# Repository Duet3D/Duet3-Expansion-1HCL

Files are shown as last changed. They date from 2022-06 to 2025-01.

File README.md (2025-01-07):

# Duet 3 Expansion 1HCL
The Duet 3 Expansion 1HCL is a CAN-FD connected expansion board for the [Duet 3 Mainboard 6HC](https://www.duet3d.com/duet3mainboard6hc), [Duet 3 Mainboard 6XD](https://www.duet3d.com/duet3mainboard6xd) and [Duet 3 Mini 5+](https://www.duet3d.com/duet3mini5plus) that is designed to provide a high current stepper motor driver, combined with multiple interfaces for position feedback. It has a number of peripheral inputs and outputs for functions such as sensing motor temperature, controlling a brake and axis endstop.

Image of Duet 3 Expansion 1HCL

Product page is here: https://www.duet3d.com/duet-3-expansion-1hcl

Documentation is here: https://docs.duet3d.com/Duet3D_hardware/Duet_3_family/Duet_3_Expansion_1HCL

As always please discuss this on the Duet3d forum: https://forum.duet3d.com/

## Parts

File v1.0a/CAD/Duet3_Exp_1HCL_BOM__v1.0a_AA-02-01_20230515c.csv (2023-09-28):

Source: | G:\My Drive\Duet\Duet3\Duet3 Expansion 1HCL\Duet3_Expansion_1HCL_v1.0a-AA-02-01\Duet3_Exp_1HCL.kicad_sch
Date: | 15/05/2023 18:52:26
Tool: | Eeschema (6.0.0)
Generator: | C:\Program Files\KiCad\bin\scripting\plugins/bom_csv_grouped_by_value_d3d.py
Component Count: | 204
Collated Components:
Item | Value | Qty | LibPart | Footprint | Reference(s) | Datasheet | Frequency | Part Number | Rating
1 | 2u2 16V 10% X5R | 4 | Device:C_Small | Capacitor_SMD:C_0603_1608Metric_Wbry | C1, C2, C26, C41 | ~ |  | CL10A225KO8NNNC
2 | 0u1 10V 10% X7R | 8 | Device:C_Small | Capacitor_SMD:C_0402_1005Metric_Wbry | C3, C4, C6, C40, C42, C44, C47, C49 | ~ |  | CL05B104KP5NNNC
3 | 470n 16V 10% X7R | 1 | Device:C_Small | Capacitor_SMD:C_0603_1608Metric_Wbry | C5 | ~ |  | CL10B474KO8NNNC
4 | 10n 25V 10% X7R | 5 | Device:C_Small | Capacitor_SMD:C_0402_1005Metric_Wbry | C7, C30, C39, C51, C63 | ~ |  | CL05B103KA5VPNC
5 | 2n2 50V 10% X7R | 2 | Device:C_Small | Capacitor_SMD:C_0402_1005Metric_Wbry | C8, C10 | ~ |  | GCM155R71H222KA37D
6 | 220n 16V 10% X7R | 4 | Device:C_Small | Capacitor_SMD:C_0603_1608Metric_Wbry | C9, C11, C14, C15 | ~ |  | CL10B224KO8NNNC
7 | 0u1 50V 10% X7R | 1 | Device:C_Small | Capacitor_SMD:C_0603_1608Metric_Wbry | C12 | ~ |  | CL10B104KB8NNNC
8 | 22n 100V 10% X7R | 1 | Device:C_Small | Capacitor_SMD:C_0603_1608Metric_Wbry | C13 | ~ |  | C0603C223K1RACTU
9 | 0u1 100V 10% X7R | 2 | Device:C_Small | Capacitor_SMD:C_0603_1608Metric_Wbry | C16, C34 | ~ |  | HMK107B7104MA-T or similar
10 | 220u 63V | 2 | Device:CP1_Small | Capacitor_SMD:CP_Elec_12.5x14 | C17, C53 |  |  | 865060762009
11 | 220n 100V 10% X7R | 4 | Device:C_Small | Capacitor_SMD:C_1206_3216Metric | C18, C19, C20, C21 | ~ |  | C3216X7R2A224K115AA
12 | 1n 100V 10% X7R | 4 | Device:C_Small | Capacitor_SMD:C_0603_1608Metric_Wbry | C22, C23, C24, C25 | ~ |  | CGA3E2X7R2A102K080AA
13 | 2u2 6.3V 10% X7R | 4 | Device:C_Small | Capacitor_SMD:C_0402_1005Metric_Wbry | C28, C50, C52, C55 | ~ |  | CC0603KRX7R5BB225
14 | 2u2 100V 10% X7R | 4 | Device:C_Small | Capacitor_SMD:C_1210_3225Metric | C29, C32, C35, C64 | ~ |  | CL32B225KCJSNNE
15 | 1u 16V 10% X7R | 4 | Device:C_Small | Capacitor_SMD:C_0603_1608Metric_Wbry | C31, C36, C38, C56 | ~ |  | CL10B105KO8NNNC
16 | 22u 100V | 1 | Device:CP1 | Capacitor_SMD:CP_Elec_8x10 | C33 |  |  | EEE-2AA220UP or similar
17 | 4u7 16V 10% X7S | 2 | Device:C_Small | Capacitor_SMD:C_1206_3216Metric | C37, C62 | ~ |  | GRM21BR71C475KE51K
18 | 10u 16V 10% X7R | 2 | Device:C_Small | Capacitor_SMD:C_0805_2012Metric | C43, C48 | ~ |  | CL21B106KOQNNNE
19 | 22p 16V 5% C0G,NP0 | 2 | Device:C_Small | Capacitor_SMD:C_0402_1005Metric_Wbry | C45, C46 | ~ |  | C0402C220J4GACTU
20 | 10n 25V 10% X7R | 1 | Duet3:C_SMALL | Capacitor_SMD:C_0402_1005Metric_Wbry | C57 |  |  | CL05B103KA5VPNC
21 | 10u 16V 10% X7R | 1 | Duet3:C_SMALL | Capacitor_SMD:C_0805_2012Metric | C58 |  |  | CL21B106KOQNNNE
22 | 0u1 10V 10% X7R | 1 | Duet3:C_SMALL | Capacitor_SMD:C_0402_1005Metric_Wbry | C59 |  |  | CL05B104KP5NNNC
23 | 22u 25V 20% X5R | 2 | Duet3:C_SMALL | Capacitor_SMD:C_0805_2012Metric | C60, C61 |  |  | GRM21BR61E226ME44L
24 | BAT40V | 4 | Diode:BAT40V | Package_TO_SOT_SMD:SOT-563 | D1, D2, D3, D4 |  |  | BAT40V-7
25 | BAT54C | 3 | Diode:BAT54C | Package_TO_SOT_SMD:SOT-23 | D6, D18, D19 | http://www.diodes.com/_files/datasheets/ds11005.pdf |  | BAT54CLT1G
26 | 60V+ 1A+ | 3 | Device:D_Schottky | Diode_SMD:D_SMF | D7, D8, D10 | ~ |  | SS1FH10-M3/H or equivalent
27 | 12V+ | 1 | Device:LED | LED_SMD:LED_0603_1608Metric | D9 | ~ |  | 150060AS75000 or equivalent Amber
28 | V_FUSED | 1 | Device:LED | LED_SMD:LED_0603_1608Metric | D11 | ~ |  | 150060BS75000 or equivalent Blue
29 | 5V+ | 1 | Device:LED | LED_SMD:LED_0603_1608Metric | D12 | ~ |  | 150060RS75000 or equivalent Red
30 | STATUS | 1 | Device:LED | LED_SMD:LED_0603_1608Metric | D13 | ~ |  | 150060RS75000 or equivalent Red
31 | ACT | 1 | Device:LED | LED_SMD:LED_0603_1608Metric | D14 | ~ |  | 150060VS75000 or equivalent Green
32 | D_TVS_5V | 1 | Device:D_Zener_Small | Diode_SMD:DFN1610-2L | D15 | ~ |  | 824032815 or 824031815
33 | D_TVS_3.3V | 1 | Device:D_Zener_Small | Diode_SMD:DFN1610-2L | D16 | ~ |  | 824032813
34 | 3.3V+ | 1 | Device:LED | LED_SMD:LED_0603_1608Metric | D17 | ~ |  | 150060VS75000 or equivalent Green
35 | V_FUSED | 1 | Device:Fuse_Small | complib:MCCQ-122-minibladefuseholder | F1 | ~ |  | Fit with 5A Fuse
36 | VB_FUSED | 1 | Device:Fuse_Small | complib:MCCQ-122-minibladefuseholder | F2 | ~ |  | Fit with 5A Fuse
37 | VSSA FUSE | 1 | Device:Fuse | Fuse:Fuse_1206_3216Metric | F3 | ~ |  | 0ZCJ0020FF2E
38 | VIN | 1 | Connector_Generic:Conn_01x02 | complib:screwt-barrier-9.5mm-1x2 | J1 | ~ |  | HB950-9.50-2P
39 | OUT_0 | 1 | Connector_Generic:Conn_01x02 | Connector_Molex:Wurth_61900211121-1x02_P2.54mm_Vertical-(Molex_KK-254_AE-6410-02Acompatible) | J2 | ~ |  | 61900211121
40 | OUT_1 | 1 | Connector_Generic:Conn_01x02 | Connector_Molex:Wurth_61900211121-1x02_P2.54mm_Vertical-(Molex_KK-254_AE-6410-02Acompatible) | J3 | ~ |  | 61900211121
41 | V_BRAKE | 1 | Connector_Generic:Conn_01x02 | Connector_JST:JST_VH_B2P-VH_1x02_P3.96mm_Vertical | J4 | ~ |  | B2P-VH(LF)(SN)
42 | IO_0 | 1 | Connector_Generic:Conn_01x05 | Connector_Molex:Wurth_61900511121-1x05_P2.54mm_Vertical(Molex_KK-254_AE-6410-05A_Compatibe) | J5 | ~ |  | 61900511121
43 | IO_1 | 1 | Connector_Generic:Conn_01x05 | Connector_Molex:Wurth_61900511121-1x05_P2.54mm_Vertical(Molex_KK-254_AE-6410-05A_Compatibe) | J6 | ~ |  | 61900511121
44 | OUT_0 Select V | 1 | Connector_Generic:Conn_01x03 | Connector_PinHeader_2.54mm:PinHeader_1x03_P2.54mm_Vertical | J7 | ~ |  | THS-03-R
45 | Q IN | 1 | Connector_Generic:Conn_01x05 | Connector_Molex:Wurth_61900511121-1x05_P2.54mm_Vertical(Molex_KK-254_AE-6410-05A_Compatibe) | J8 | ~ |  | 61900511121
46 | SPI | 1 | Connector_Generic:Conn_02x05_Odd_Even | Connector_IDC:IDC-Header_2x05_P2.54mm_Vertical | J9 | ~ |  | 61201021621
47 | SWD | 1 | Connector_Generic:Conn_01x06 | complib:JST_ZH_1x06_P1.5_B6B-ZR-SM4-TF | J10 | ~ |  | B6B-ZR(LF)(SN)
48 | DRIVER | 1 | Connector_Generic:Conn_01x04 | Connector_JST:JST_VH_B4P-VH_1x04_P3.96mm_Vertical | J11 | ~ |  | B4P-VH(LF)(SN)
49 | TEMP_0 | 1 | Connector_Generic:Conn_01x02 | Connector_Molex:Wurth_61900211121-1x02_P2.54mm_Vertical-(Molex_KK-254_AE-6410-02Acompatible) | J12 | ~ |  | 61900511121
50 | CAN_IN | 1 | Duet3:RJ12-Connector_Specialized | complib:RJ11_6P6C_half_shield | J13 |  |  | Wurth 615 006 143 421 or equivalent
51 | CAN_OUT | 1 | Duet3:RJ12-Connector_Specialized | complib:RJ11_6P6C_half_shield | J14 |  |  | Wurth 615 006 143 421 or equivalent
52 | OUT_1 Select V | 1 | Connector_Generic:Conn_01x03 | Connector_PinHeader_2.54mm:PinHeader_1x03_P2.54mm_Vertical | J15 | ~ |  | THS-03-R
53 | TEMP_1 | 1 | Connector_Generic:Conn_01x02 | Connector_Molex:Wurth_61900211121-1x02_P2.54mm_Vertical-(Molex_KK-254_AE-6410-02Acompatible) | J16 | ~ |  | 61900511121
54 | Term_R | 1 | Duet3:Jumper_4_Open | Connector_PinHeader_2.54mm:PinHeader_1x04_P2.54mm_Vertical | JP1 | ~ |  | THS-04-R
55 | CAN RESET | 1 | Device:Jumper_NO_Small | Connector_PinHeader_2.54mm:PinHeader_1x02_P2.54mm_Vertical | JP2 |  |  | THS-02-R
56 | IO1_I2C | 1 | Device:Jumper_NO_Small | Connector_PinHeader_2.54mm:PinHeader_1x02_P2.54mm_Vertical | JP3 |  |  | THS-02-R
57 | CM Choke | 1 | Duet3:L_Coupled_v2 | complib:Wurth_CM_Choke_1812_744235nnn | L1 | ~ |  | 744235110
58 | 4.7uH | 1 | Device:L_Small | Inductor_SMD:L_0805_2012Metric | L2 | ~ |  | MBKK2012T4R7M or CB2012T4R7M or similar
59 | 120R @100mHz | 2 | Device:L_Small | Inductor_SMD:L_0402_1005Metric | L3, L5 | ~ |  | 7427927311 or similar
60 | 100u | 1 | Device:L_Small | Inductor_SMD:L_Taiyo-Yuden_NR-60xx | L4 | ~ |  | NR6028T101M | >0.5A, >0.6A saturation, shielded, <0R85 DCR
61 | 1K @100Mhz | 1 | Device:L_Small | Inductor_SMD:L_0603_1608Metric | L6 | ~ |  | 742792662 or PE-0603FB102ST or similar
62 | 100 ohm, 4 A | 2 | Duet3:L_MINI | Inductor_SMD:L_0805_2012Metric | L7, L9 |  |  | 742792025 or MPZ2012S101A or similar
63 | 10u | 1 | Duet3:L_MINI | Inductor_SMD:L_Wuerth_7440405xxxx | L8 |  |  | 74404054100 or NR5040T100M
64 | FID | 2 | Duet3:FID | Fiducial:Fiducial_1mm_Mask2mm | M1, M2 |  |  | virtual component - DNP
65 | MOUNTING | 4 | Mechanical:MountingHole | MountingHole:MountingHole_3.2mm_M3 | M3, M4, M5, M6 | ~ |  | virtual component - DNP
66 | Duet3D_Logo | 1 | Duet3:Duet3D_Logo | complib:LOGO_NEW_Duet3D_vertical_6mm | M7 |  |  | virtual component - DNP
67 | GNDANA-GND NET TIE | 1 | Device:Net-Tie_2 | NetTie:NetTie-2_SMD_Pad0.5mm | NT1 |  |  | virtual component - DNP
68 | SIZ250DT | 4 | Duet3:SIZ250DT | complib:Vishay_PowerPAIR3x3S | Q1, Q2, Q3, Q4 | https://www.infineon.com/dgdl/irfi4019h-117p.pdf?fileId=5546d462533600a401535623d74d1f6f |  | SIZ250DT-T1-GE3
69 | DMN6040SVT | 2 | Duet3:DMN6040SVT | Package_TO_SOT_SMD:SOT-23-6-DMN6040SVT | Q5, Q6 | https://www.diodes.com/assets/Datasheets/DMN6040SVT.pdf |  | DMN6040SVT
70 | 2R2 1% 0.063W | 1 | Device:R_Small | Resistor_SMD:R_0402_1005Metric_Wbry | R1 | ~ |  | RMCF0402FT2R20
71 | 59R 1% 0.063W | 2 | Device:R_Small | Resistor_SMD:R_0402_1005Metric_Wbry | R2, R3 | ~ |  | RMCF0402FT59R0
72 | 47R 1% 0.063W | 4 | Device:R_Small | Resistor_SMD:R_0603_1608Metric_Wbry | R4, R5, R6, R7 | ~ |  | RMCF0402FT47R0
73 | 150R 1% 0.063W | 8 | Device:R_Small | Resistor_SMD:R_0402_1005Metric_Wbry | R8, R9, R10, R11, R12, R13, R14, R15 | ~ |  | RMCF0402FT150R
74 | 0R05 1% 1W | 2 | Duet3:R_SenseKelvin | complib:R_1206_SenseResistorKelvin | R16, R17 |  |  | PE1206FRE470R05L or ERJ-8CWFR050V or similar
75 | 10K 1% 0.1W | 19 | Device:R_Small | Resistor_SMD:R_0402_1005Metric_Wbry | R18, R19, R20, R21, R22, R27, R38, R39, R42, R43, R46, R47, R64, R65, R66, R67, R68, R69, R72 | ~ |  | RK73H1ETTP1002F
76 | 27R 1% 0.063W | 1 | Device:R_Small | Resistor_SMD:R_0402_1005Metric_Wbry | R23 | ~ |  | CRGCQ0402F27R
77 | 470R 1% 0.063W | 5 | Device:R_Small | Resistor_SMD:R_0402_1005Metric_Wbry | R24, R25, R45, R49, R57 | ~ |  | RC0402FR-07470RL
78 | 4K7 1% 0.063W | 2 | Device:R_Small | Resistor_SMD:R_0402_1005Metric_Wbry | R26, R50 | ~ |  | RK73H1ETTP4701F
79 | 100K 1% 0.063W | 2 | Device:R_Small | Resistor_SMD:R_0402_1005Metric_Wbry | R28, R34 | ~ |  | RMCF0402FT100K
80 | 5K1 1% 0.063W | 1 | Device:R_Small | Resistor_SMD:R_0402_1005Metric_Wbry | R29 | ~ |  | RMCF0402FT5K10
81 | 0R5 1% 0.125W | 1 | Device:R_Small | Resistor_SMD:R_0402_1005Metric_Wbry | R30 | ~ |  | CSR0402FKR500
82 | 0R | 1 | Device:R_Small | Resistor_SMD:R_0402_1005Metric_Wbry | R31 | ~ |  | RMCF0402ZT0R00
83 | 316K 1% 0.063W | 1 | Device:R_Small | Resistor_SMD:R_0402_1005Metric_Wbry | R32 | ~ |  | RC0402FR-07316KL
84 | 25K5 1% 0.063W | 1 | Device:R_Small | Resistor_SMD:R_0402_1005Metric_Wbry | R33 | ~ |  | AC0402FR-0725K5L
85 | 10K 1% 0.33W | 1 | Duet3:R_SMALL | Resistor_SMD:R_0805_2012Metric | R35 |  |  | CRGH0805F10K
86 | 2K2 1% 0.063W | 2 | Duet3:R_SMALL | Resistor_SMD:R_0402_1005Metric_Wbry | R36, R54 |  |  | RK73H1ETTP2201F
87 | 1K 1% 0.063W | 4 | Device:R_Small | Resistor_SMD:R_0402_1005Metric_Wbry | R37, R40, R48, R51 | ~ |  | RMCF0402FT1K00
88 | 2K2 0.1% 0.2W | 2 | Device:R_Small | Resistor_SMD:R_0603_1608Metric_Wbry | R41, R73 | ~ |  | RMCF0402FT2K20
89 | 27R 1% 0.063W | 1 | Duet3:R_SMALL | Resistor_SMD:R_0402_1005Metric_Wbry | R44 |  |  | CRGCQ0402F27R | 0.1W+
90 | 180R 1% 0.063W | 1 | Device:R_Small | Resistor_SMD:R_0402_1005Metric_Wbry | R52 | ~ |  | RMCF0402FT180R
91 | 10K 1% 0.1W | 1 | Duet3:R_SMALL | Resistor_SMD:R_0402_1005Metric_Wbry | R53 |  |  | RK73H1ETTP1002F
92 | 100R 1% 0.063W | 3 | Device:R_Small | Resistor_SMD:R_0402_1005Metric_Wbry | R55, R56, R58 | ~ |  | CRGCQ0402F100R
93 | 60K4 1% 0.063W | 1 | Device:R_Small | Resistor_SMD:R_0402_1005Metric_Wbry | R60 | ~ |  | RMCF0402FT60K4
94 | 4K7 1% 0.063W | 2 | Duet3:R_SMALL | Resistor_SMD:R_0402_1005Metric_Wbry | R61, R62 |  |  | RK73H1ETTP4701F
95 | 180R 1% 0.063W | 1 | Duet3:R_SMALL | Resistor_SMD:R_0402_1005Metric_Wbry | R63 |  |  | RMCF0402FT180R
96 | 16K 1% 0.063W | 1 | Duet3:R_SMALL | Resistor_SMD:R_0402_1005Metric_Wbry | R70 |  |  | RMCF0402FT16K0
97 | 5K1 1% 0.063W | 1 | Duet3:R_SMALL | Resistor_SMD:R_0402_1005Metric_Wbry | R71 |  |  | RMCF0402FT5K10
98 | ATSAME51G19A | 1 | MCU_Microchip_SAME:ATSAME51G19A | Package_DFN_QFN:QFN-48-1EP_7x7mm_P0.5mm_EP5.2x5.2mm_ThermalVias | U1 |  |  | ATSAME51G19A
99 | TMC2160 | 1 | Duet3:TMC2160-TA | complib:TMC5160-TA | U2 | https://www.trinamic.com/products/integrated-circuits/details/tmc2160-ta/ |  | TMC2160A-TA
100 | AP7366-W5-7 | 1 | Duet3:AP7366-33W5-7 | Package_TO_SOT_SMD:SOT-23-5 | U3 | https://www.diodes.com/assets/Datasheets/AP7366.pdf |  | AP7366-W5-7
101 | MAX15062C | 1 | Regulator_Switching:MAX15062C | Package_DFN_QFN:DFN-8_2x2mm_P0.5mm | U4 | http://datasheets.maximintegrated.com/en/ds/MAX15062.pdf |  | MAX15062C
102 | MCP2542 | 1 | Duet3:MCP2542 | Package_DFN_QFN:DFN-8-1EP_3x2mm_P0.5mm_EP1.3x1.5mm | U5 |  |  | MCP2542FDT-E/MNY
103 | TS30041 | 1 | Duet3:TS30042 | Package_DFN_QFN:QFN-16-1EP_3x3mm_P0.5mm_EP1.8x1.8mm_ThermalVias | U6 |  |  | TS30041-M000QFNR
104 | CRYSTAL_4PIN | 1 | Duet3:CRYSTAL_4PIN | complib:Crystal_SMD_ECS-33B-4Pin_3.2x2.5mm | X1 |  | 25MHz | TSX-3225 25.0000MF10P

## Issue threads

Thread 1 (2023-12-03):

Oscillator

RudolphRiedel, 2023-12-03:
Not really an issue, more an interested inquiry as I am also using ATSAME51 and ATSAMC21 for quite some time now.
I have not checked the software, if there is any to take a peek at, I just came across this repository.

Are you really ok with the TSX-3225 25.0000MF10P and the 22pF capacitors for it when running CAN-FD?
First of all this crystal has a load capacitance of 18pF and using the "Load Capacitance Equation" in the SAM E51 family datasheet, using 27pF would be a bit more apropriate.
This is only a minor deviation, but does the CAN-FD really work with up to 8MBit/s with this while sending out 64 byte packages?

And on a first glance I found the 25MHz odd for the crystal as I usually go with 16MHz and I know that the PLL has a maximum
input frequency of 3.2MHz.
But well, setting DPLLCTRLB.DIV to 4 gives a clock divider of 10 and so a multiplier of 48 to get to 120MHz can be used.
And a multplier of 32 on the second PLL for the CAN module to be clocked at 80Mhz or perhaps 40 to use the maximum input clock of 100MHz for the CAN, ADC and SERCOM modules.

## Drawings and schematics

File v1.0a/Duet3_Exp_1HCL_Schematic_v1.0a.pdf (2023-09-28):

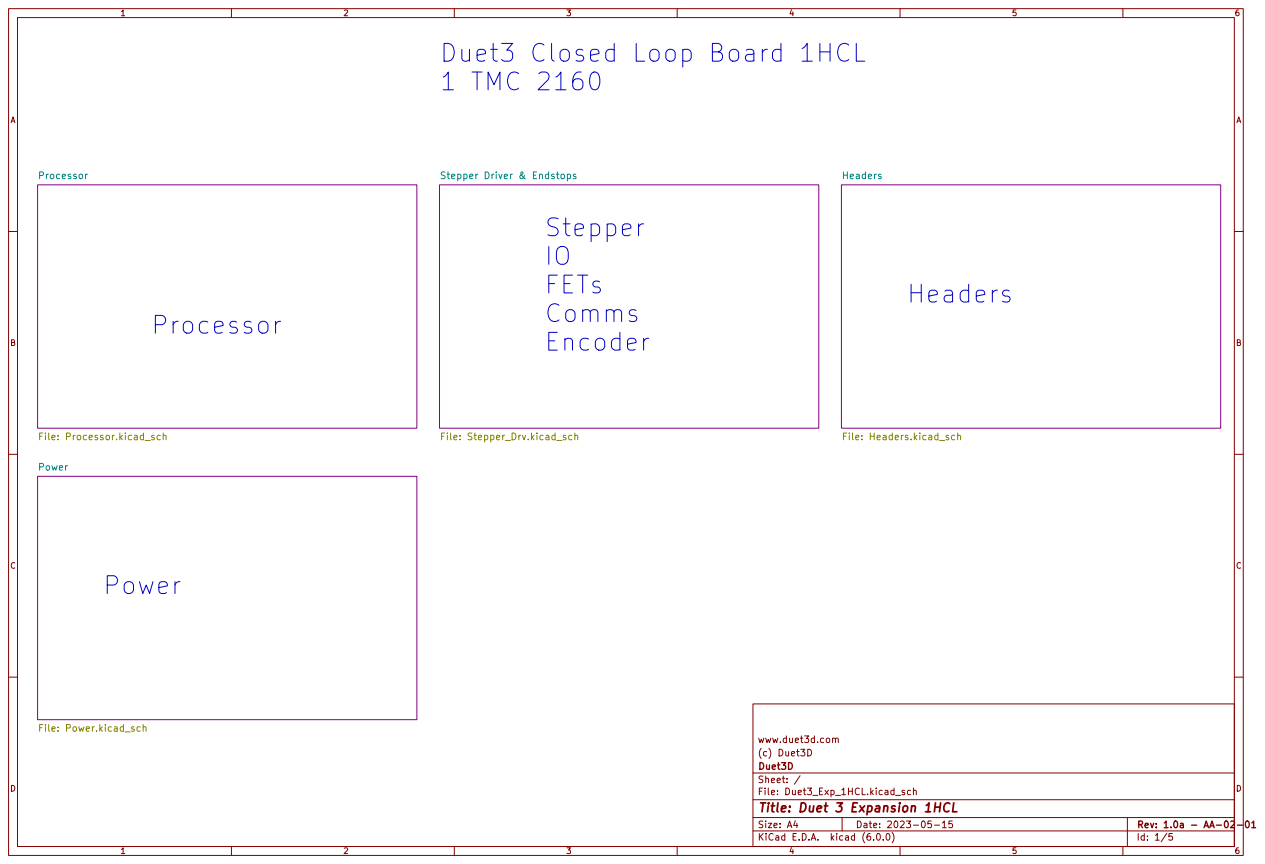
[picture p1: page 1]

Id: 1/5 Title: Duet 3 Expansion 1HCL

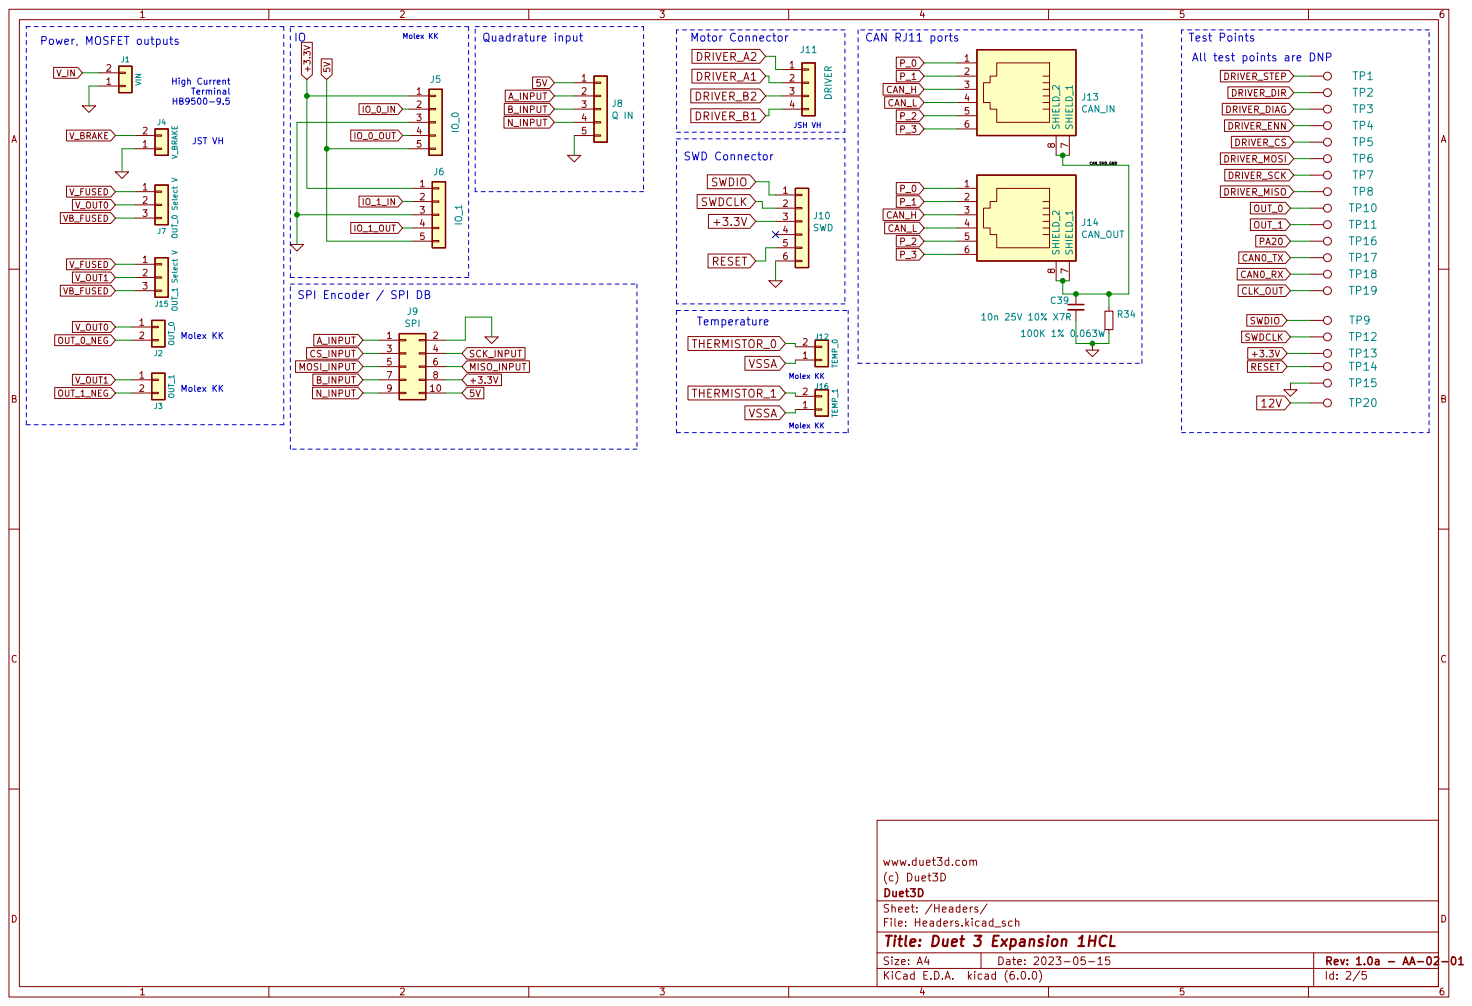
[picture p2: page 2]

JSH VH Power, MOSFET outputs

Molex KK Molex KK High Current Terminal HB9500-9.5

P_3 DRIVER_B1

4 IO_0_OUT

CAN_SHD_GND SPI Encoder / SPI DB

www.duet3d.com
(c) Duet3D
File: Headers.kicad_sch Sheet: /Headers/ Duet3D

Id: 2/5 Title: Duet 3 Expansion 1HCL

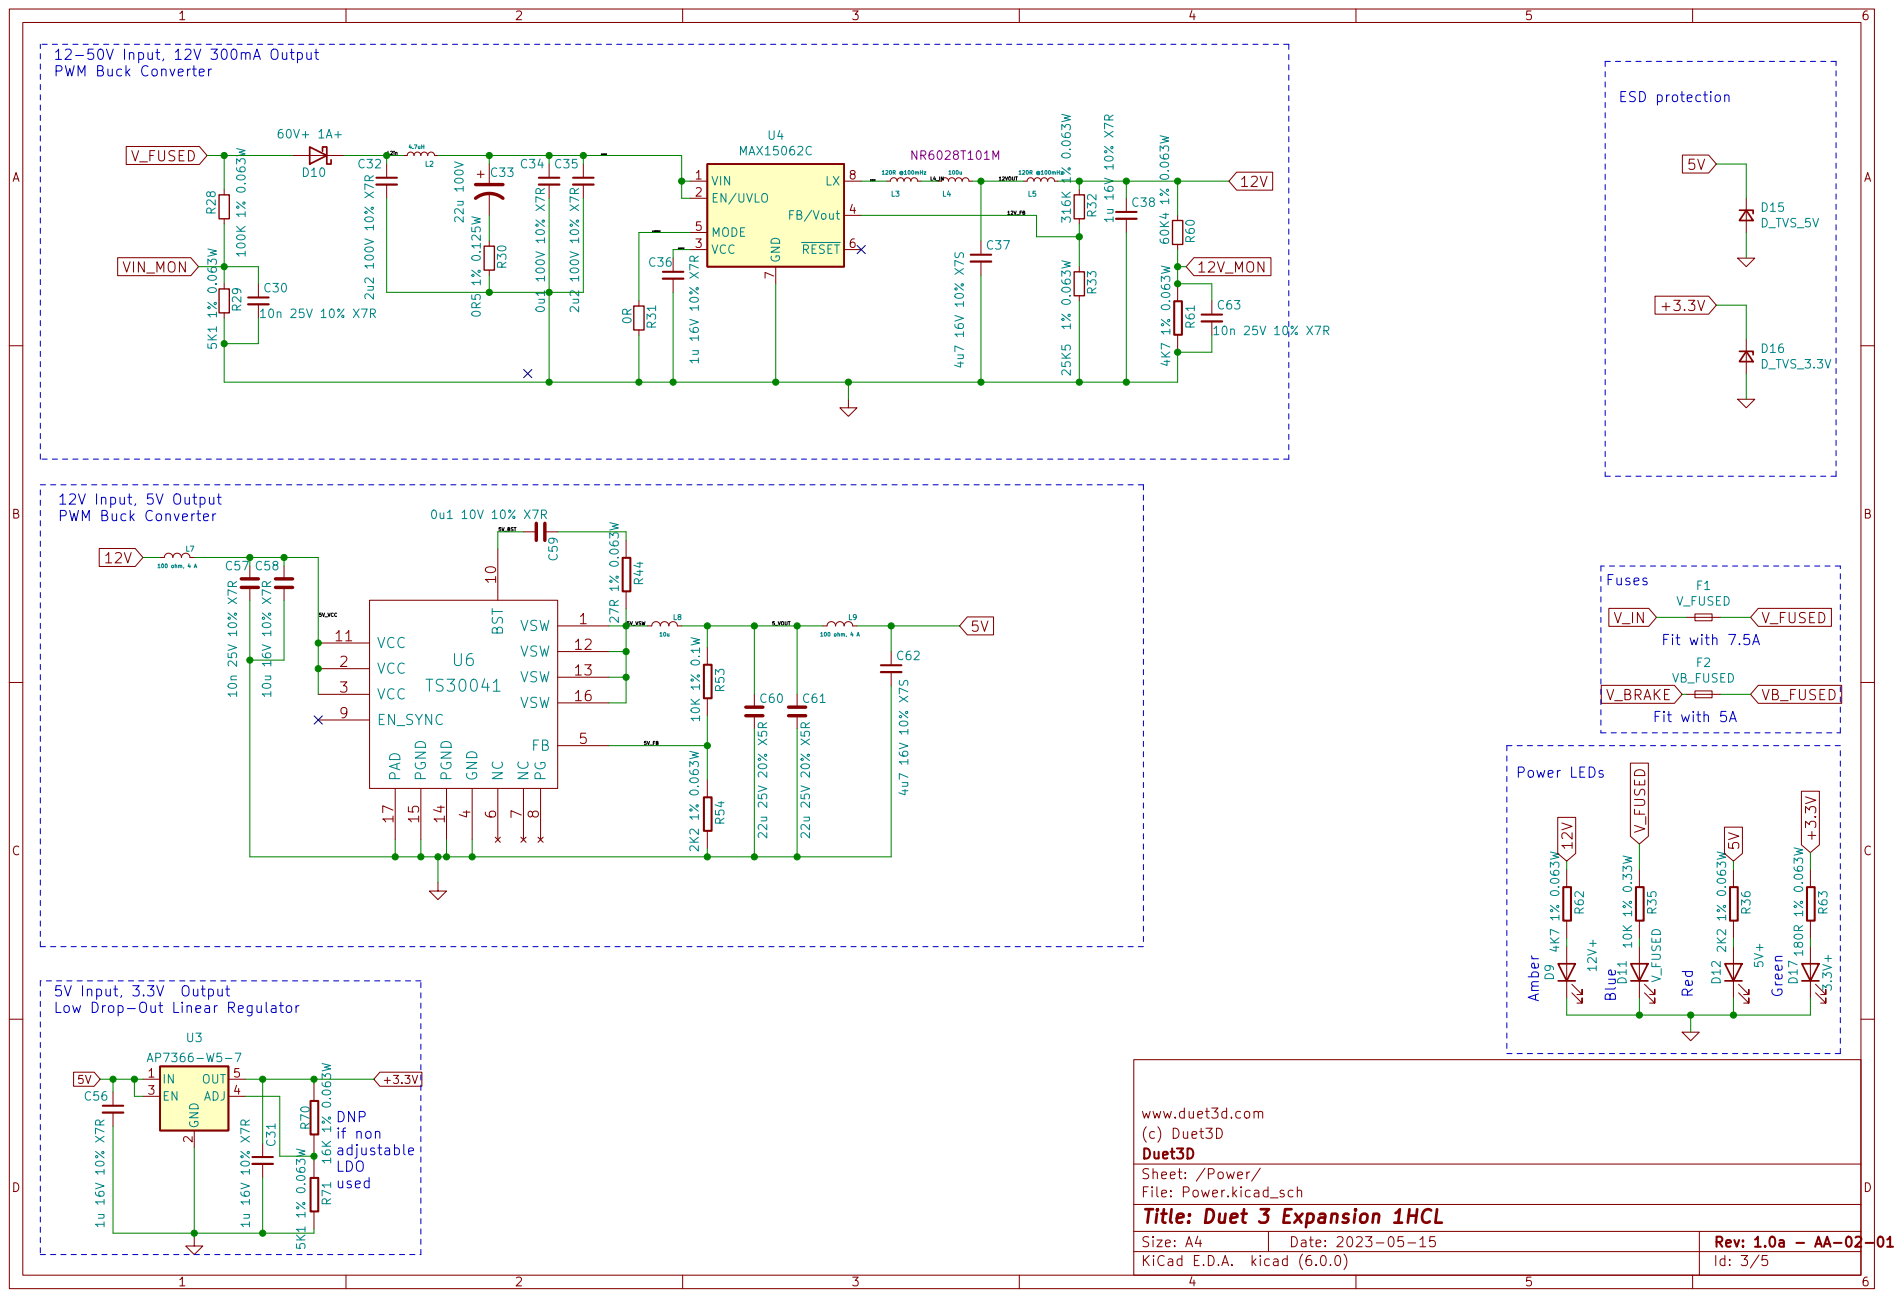
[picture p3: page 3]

5V Input, 3.3V Output
Low Drop-Out Linear Regulator

(c) Duet3D
File: Power.kicad_sch Sheet: /Power/ Duet3D

Id: 3/5 Title: Duet 3 Expansion 1HCL

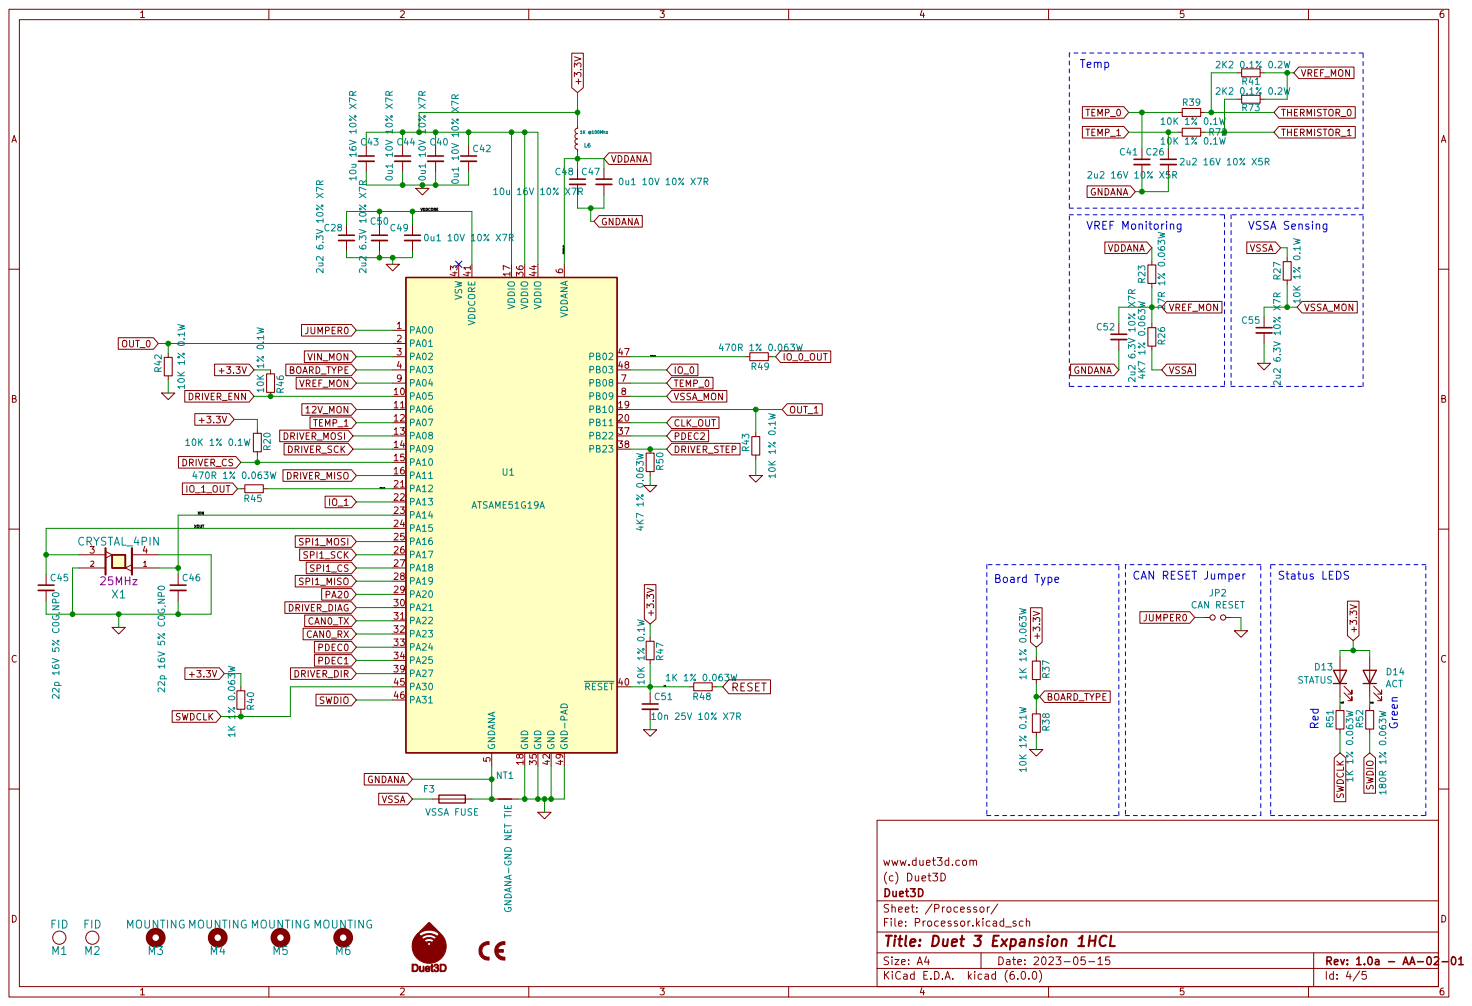
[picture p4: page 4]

CAN RESET Jumper JP2 CAN RESET R37 1K 1% 0.063W

(c) Duet3D

File: Processor.kicad_sch Sheet: /Processor/ Duet3D

Id: 4/5 Title: Duet 3 Expansion 1HCL

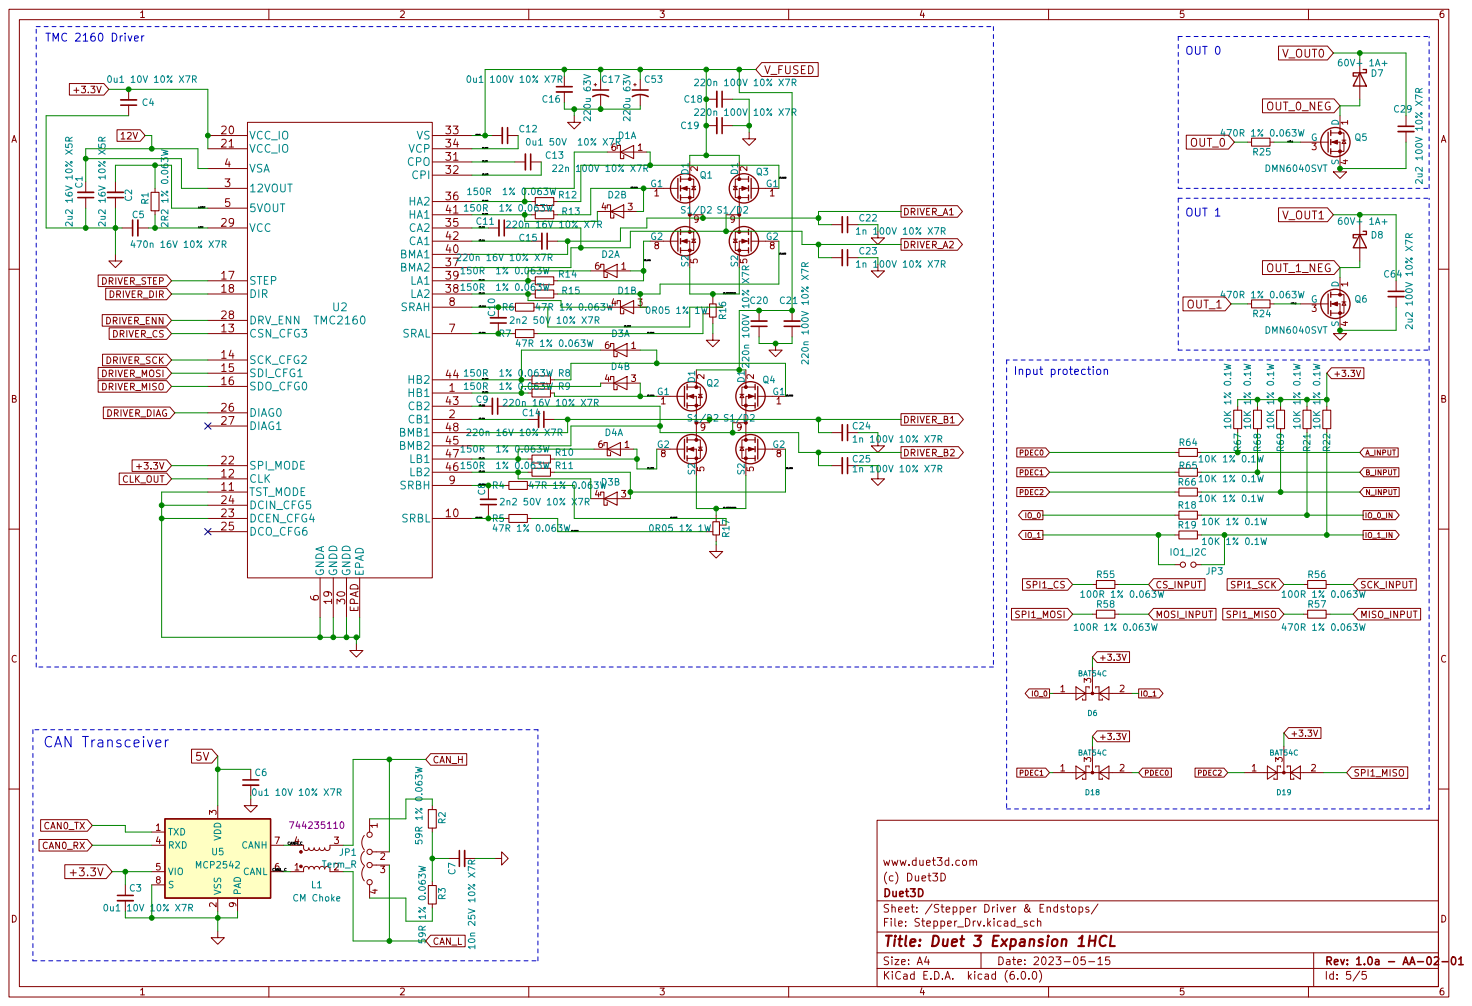
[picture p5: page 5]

6 SRAL 7 SRAH 8 SRBH 9 EPAD EPAD U2 TMC2160 R14 150R 1% 0.063W

3 RXD 4 VIO 5 CANL 6 CANH 7 S

(c) Duet3D
Sheet: /Stepper Driver & Endstops/ Duet3D

File: Stepper_Drv.kicad_sch
Id: 5/5 Title: Duet 3 Expansion 1HCL

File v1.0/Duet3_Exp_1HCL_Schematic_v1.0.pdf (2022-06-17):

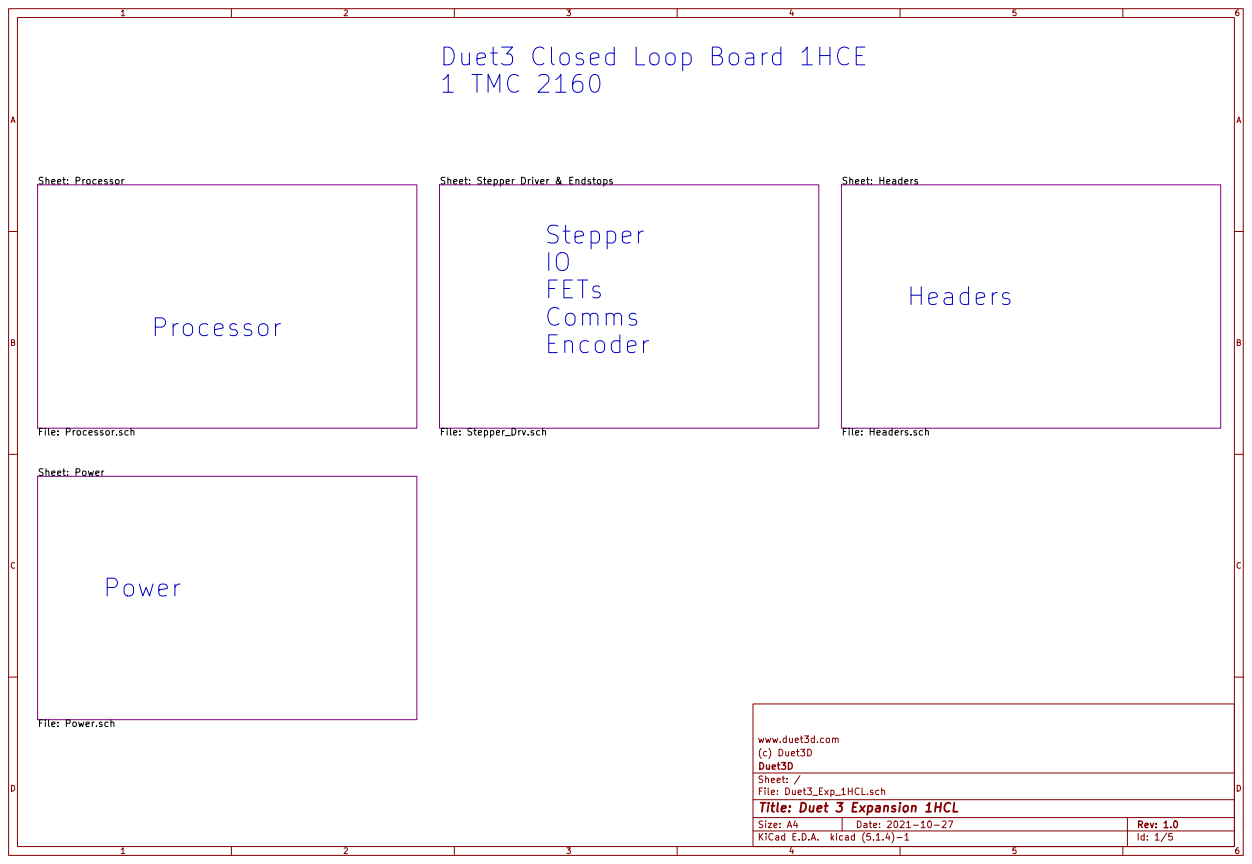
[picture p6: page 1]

Sheet: Stepper Driver & Endstops

Id: 1/5 Title: Duet 3 Expansion 1HCL

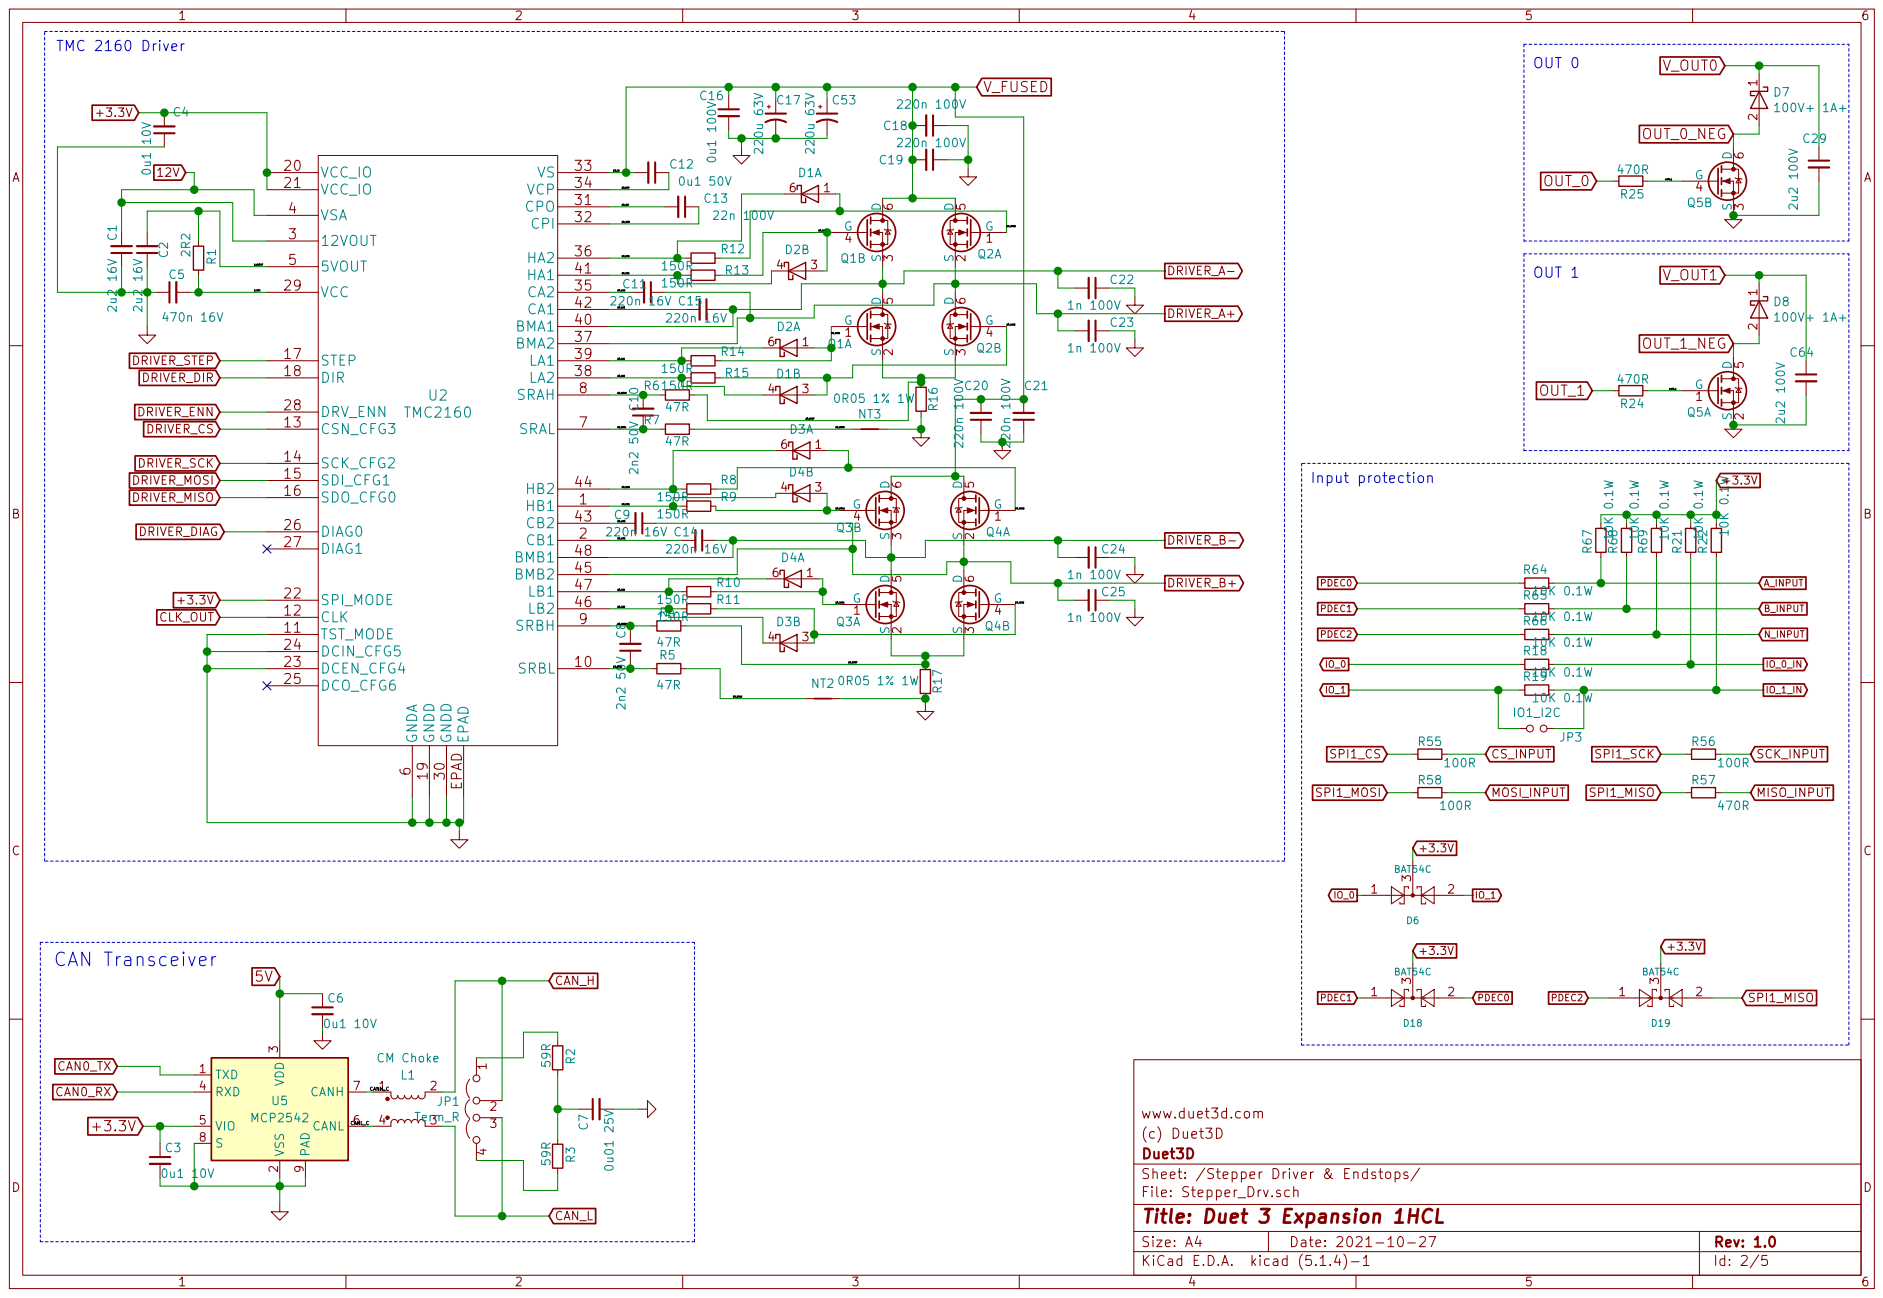
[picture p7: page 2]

6 SRAL 7 SRAH 8 SRBH 9 EPAD EPAD U2 TMC2160 C64 2u2 100V R57

3 RXD 4 VIO 5 CANL 6 CANH 7 S

www.duet3d.com
(c) Duet3D
Sheet: /Stepper Driver & Endstops/ Duet3D

File: Stepper_Drv.sch
Id: 2/5 Title: Duet 3 Expansion 1HCL

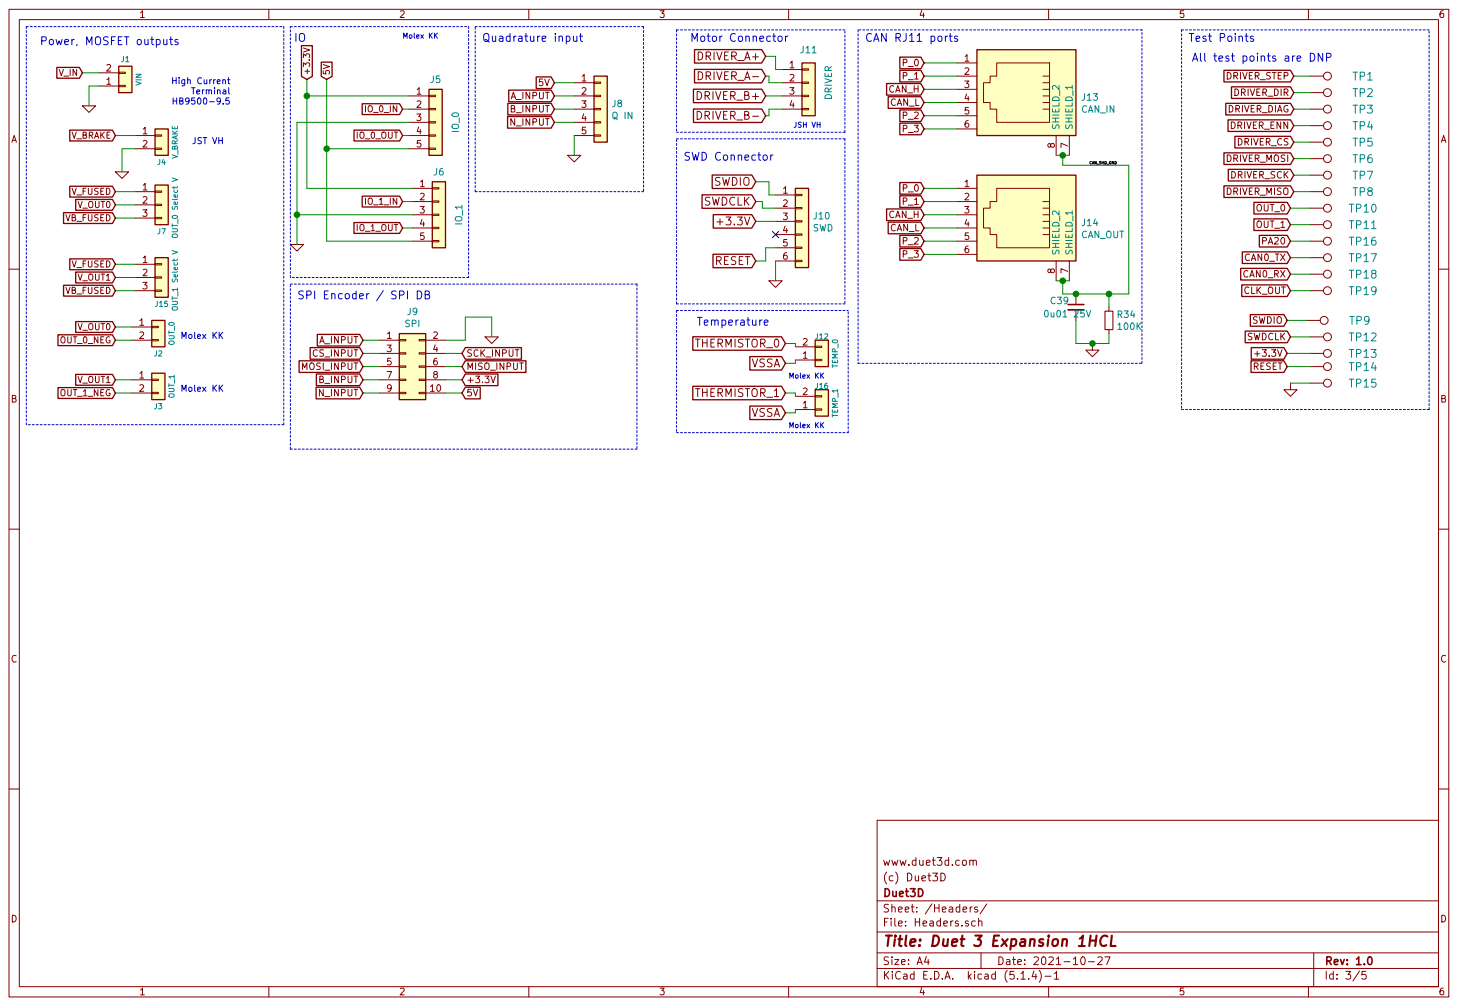
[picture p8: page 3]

Molex KK SWD Connector

SPI Encoder / SPI DB

www.duet3d.com
(c) Duet3D
File: Headers.sch Sheet: /Headers/ Duet3D

Id: 3/5 Title: Duet 3 Expansion 1HCL

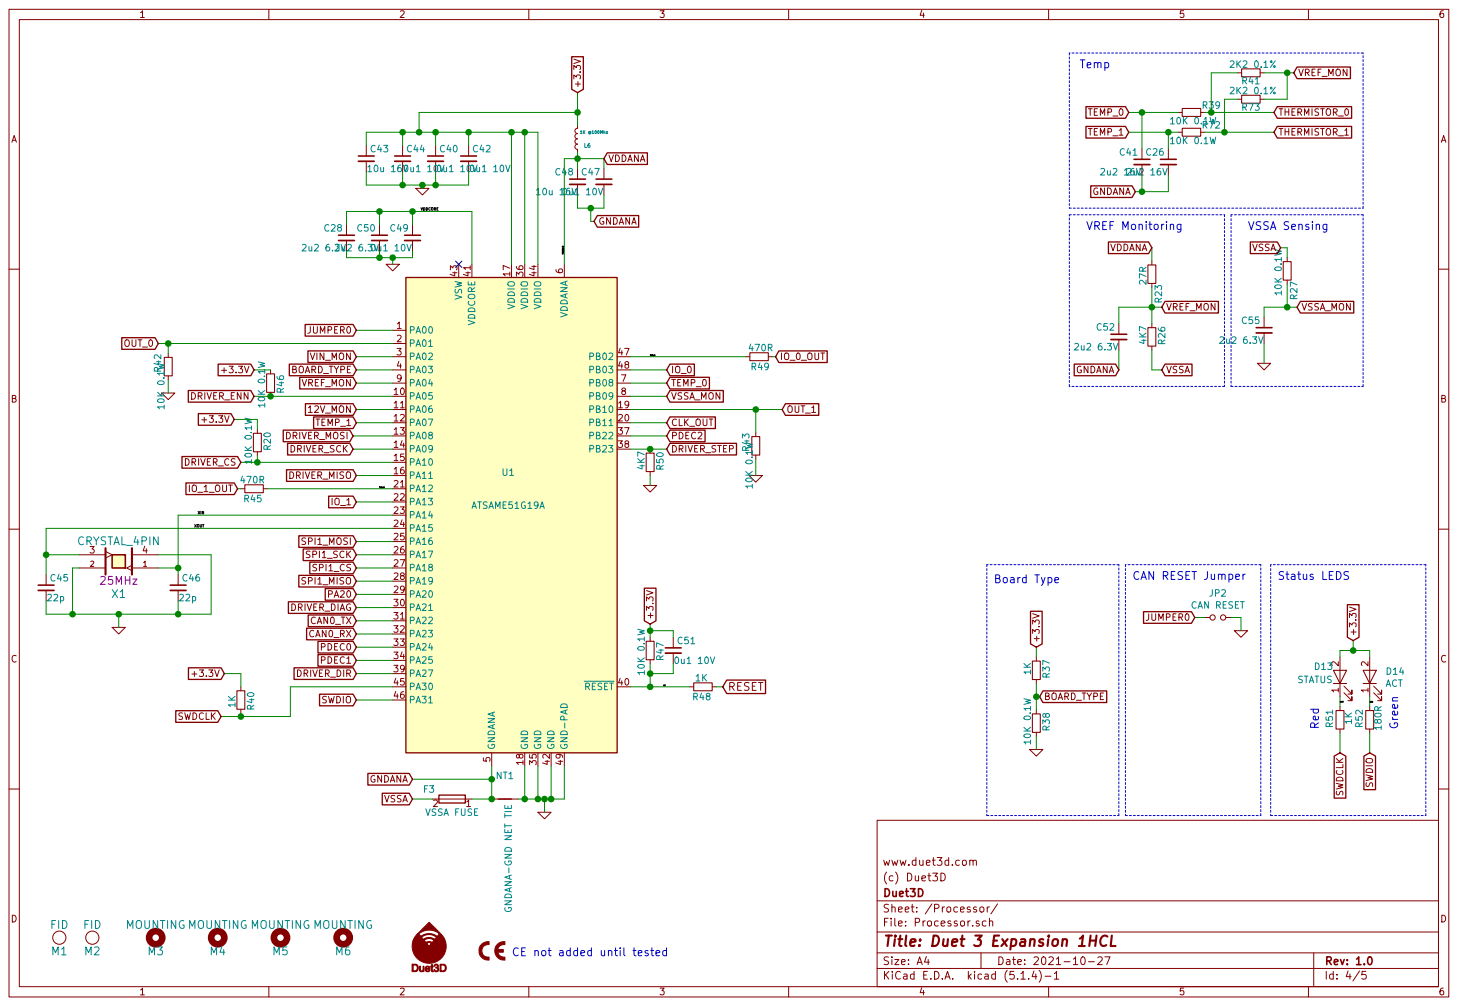
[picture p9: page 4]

www.duet3d.com
(c) Duet3D
File: Processor.sch Sheet: /Processor/ Duet3D

Id: 4/5 Title: Duet 3 Expansion 1HCL

CE not added until tested

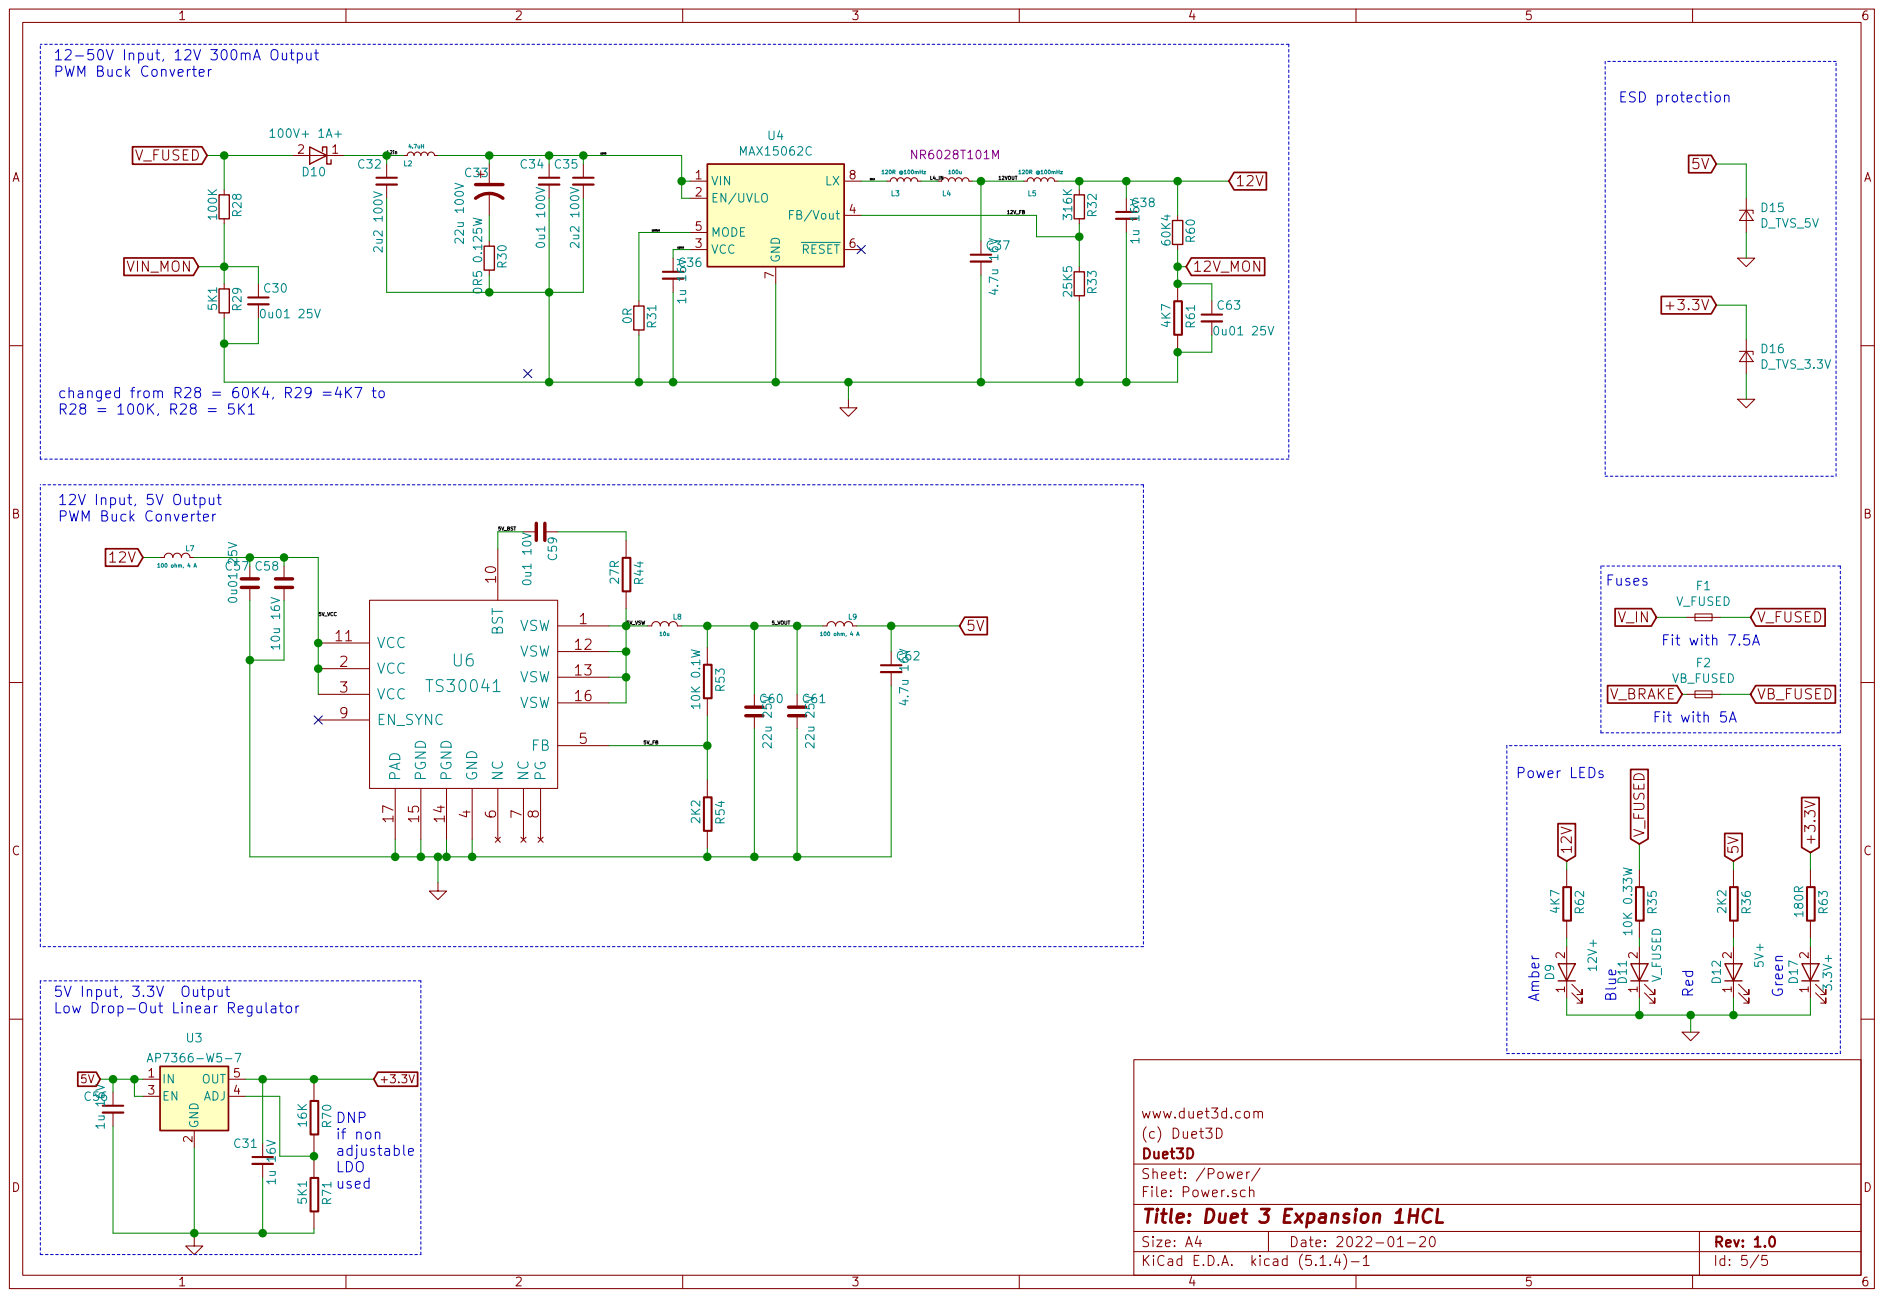
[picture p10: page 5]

www.duet3d.com
(c) Duet3D
File: Power.sch Sheet: /Power/ Duet3D

Id: 5/5 Title: Duet 3 Expansion 1HCL

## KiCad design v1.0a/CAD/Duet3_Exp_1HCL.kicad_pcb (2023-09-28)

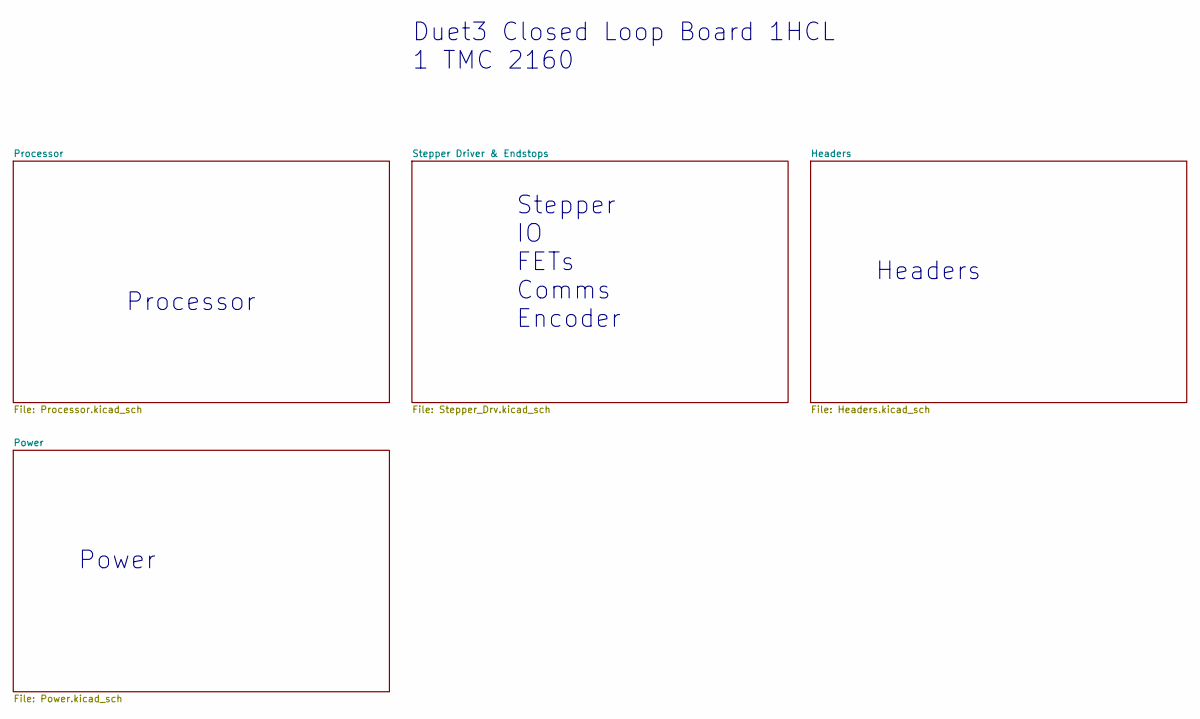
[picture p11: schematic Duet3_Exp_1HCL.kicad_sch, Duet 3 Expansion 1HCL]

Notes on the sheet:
Power
Duet3 Closed Loop Board 1HCL 1 TMC 2160
Processor
Stepper IO FETs Comms Encoder
Headers

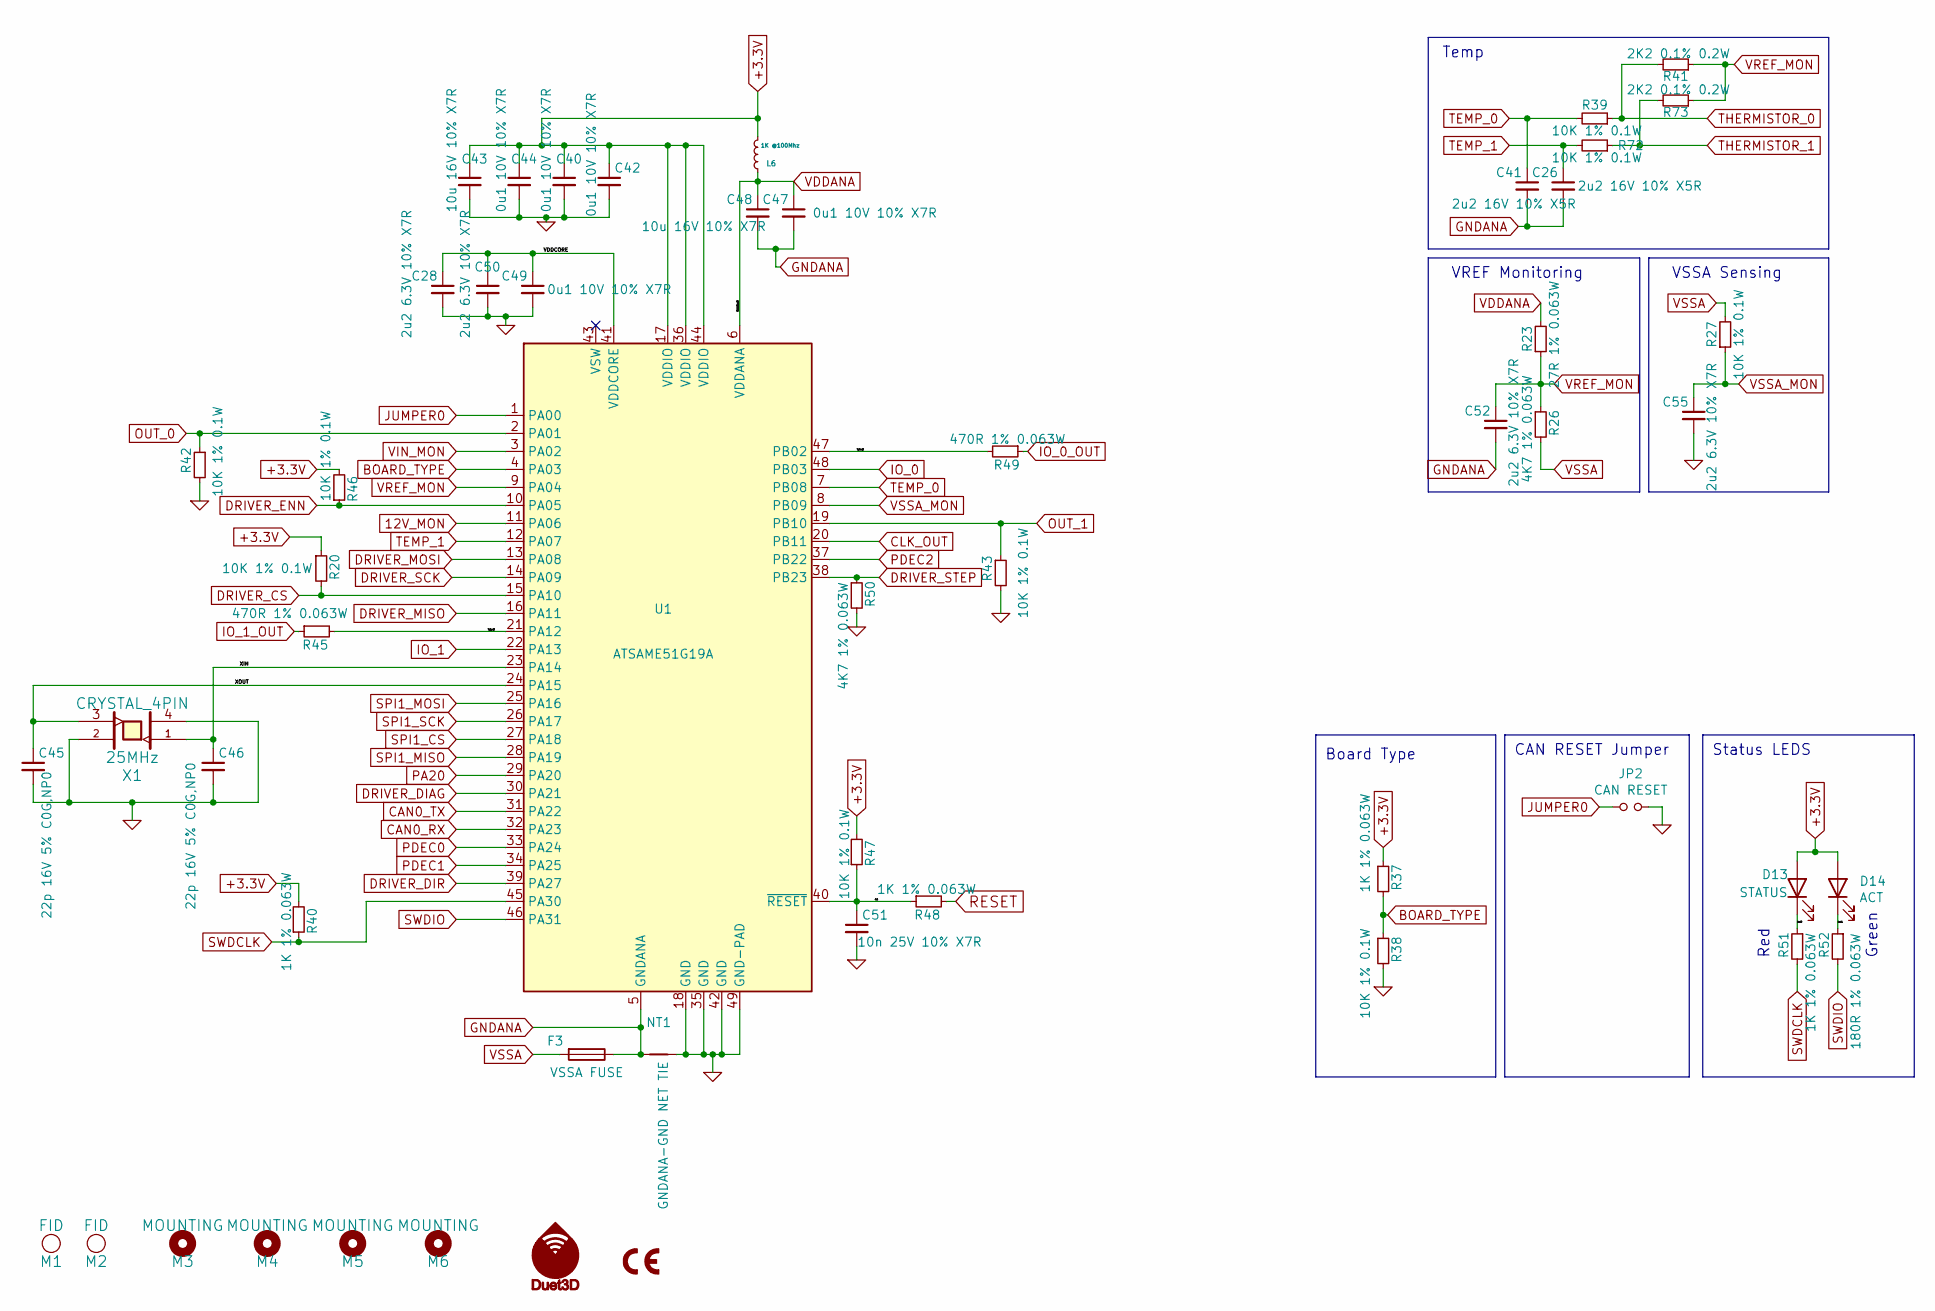
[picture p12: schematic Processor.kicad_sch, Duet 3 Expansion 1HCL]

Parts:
C26, C41: 2u2 16V 10% X5R; C_0603_1608Metric_Wbry; Part Number CL10A225KO8NNNC
C28, C50, C52, C55: 2u2 6.3V 10% X7R; C_0402_1005Metric_Wbry; Part Number CC0603KRX7R5BB225
C40, C42, C44, C47, C49: 0u1 10V 10% X7R; C_0402_1005Metric_Wbry; Part Number CL05B104KP5NNNC
C43, C48: 10u 16V 10% X7R; C_0805_2012Metric; Part Number CL21B106KOQNNNE
C45, C46: 22p 16V 5% C0G,NP0; C_0402_1005Metric_Wbry; Part Number C0402C220J4GACTU
C51: 10n 25V 10% X7R; C_0402_1005Metric_Wbry; Part Number CL05B103KA5VPNC
D13: STATUS; LED_0603_1608Metric; Part Number 150060RS75000 or equivalent Red
D14: ACT; LED_0603_1608Metric; Part Number 150060VS75000 or equivalent Green
F3: VSSA FUSE; Fuse_1206_3216Metric; Part Number 0ZCJ0020FF2E
JP2: CAN RESET; PinHeader_1x02_P2.54mm_Vertical; Part Number THS-02-R
L6: 1K @100Mhz; L_0603_1608Metric; Part Number 742792662 or PE-0603FB102ST or similar
M1, M2: FID; Fiducial_1mm_Mask2mm; Part Number virtual component - DNP
M3, M4, M5, M6: MOUNTING; MountingHole_3.2mm_M3; Part Number virtual component - DNP
M7: Duet3D_Logo; LOGO_NEW_Duet3D_vertical_6mm; Part Number virtual component - DNP
NT1: GNDANA-GND NET TIE; NetTie-2_SMD_Pad0.5mm; Part Number virtual component - DNP
R20, R27, R38, R39, R42, R43, R46, R47, R72: 10K 1% 0.1W; R_0402_1005Metric_Wbry; Part Number RK73H1ETTP1002F
R23: 27R 1% 0.063W; R_0402_1005Metric_Wbry; Part Number CRGCQ0402F27R
R26, R50: 4K7 1% 0.063W; R_0402_1005Metric_Wbry; Part Number RK73H1ETTP4701F
R37, R40, R48, R51: 1K 1% 0.063W; R_0402_1005Metric_Wbry; Part Number RMCF0402FT1K00
R41, R73: 2K2 0.1% 0.2W; R_0603_1608Metric_Wbry; Part Number RMCF0402FT2K20
R45, R49: 470R 1% 0.063W; R_0402_1005Metric_Wbry; Part Number RC0402FR-07470RL
R52: 180R 1% 0.063W; R_0402_1005Metric_Wbry; Part Number RMCF0402FT180R
U1: ATSAME51G19A; QFN-48-1EP_7x7mm_P0.5mm_EP5.2x5.2mm_ThermalVias; Part Number ATSAME51G19A
X1: CRYSTAL_4PIN; Crystal_SMD_ECS-33B-4Pin_3.2x2.5mm; Part Number TSX-3225 25.0000MF10P

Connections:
12V_MON: U1.11 (PA06); also elsewhere on the board
+3.3V: C40.1, C42.1, C43.1, C44.1, D13.2 (A), D14.2 (A), L6.1, R20.1, R37.1, R40.2, R46.2, R47.2, U1.17 (VDDIO), U1.36 (VDDIO), U1.44 (VDDIO); also elsewhere on the board
/Processor/VDDCORE: C28.1, C49.1, C50.1, U1.41 (VDDCORE)
/Processor/XIN: C46.1, U1.23 (PA14), X1.1
/Processor/XOUT: C45.1, U1.24 (PA15), X1.3
/Processor/io0out: R49.2, U1.47 (PB02)
/Processor/io1out: R45.2, U1.21 (PA12)
/Processor/led0: D13.1 (K), R51.1
/Processor/led1: D14.1 (K), R52.1
/Processor/rst: C51.1, R47.1, R48.1, U1.40 (~RESET)
BOARD_TYPE: R37.2, R38.1, U1.4 (PA03)
CAN0_RX: U1.32 (PA23); also elsewhere on the board
CAN0_TX: U1.31 (PA22); also elsewhere on the board
CLK_OUT: U1.20 (PB11); also elsewhere on the board
DRIVER_CS: R20.2, U1.15 (PA10); also elsewhere on the board
DRIVER_DIAG: U1.30 (PA21); also elsewhere on the board
DRIVER_DIR: U1.39 (PA27); also elsewhere on the board
DRIVER_ENN: R46.1, U1.10 (PA05); also elsewhere on the board
DRIVER_MISO: U1.16 (PA11); also elsewhere on the board
DRIVER_MOSI: U1.13 (PA08); also elsewhere on the board
DRIVER_SCK: U1.14 (PA09); also elsewhere on the board
DRIVER_STEP: R50.1, U1.38 (PB23); also elsewhere on the board
GND: C28.2, C40.2, C42.2, C43.2, C44.2, C45.2, C46.2, C49.2, C50.2, C51.2, C55.2, JP2.2, NT1.2, R38.2, R42.2, R43.2, R50.2, U1.18 (GND), U1.35 (GND), U1.42 (GND), U1.49 (GND-PAD), X1.2, X1.4; also elsewhere on the board
GNDANA: C26.2, C41.2, C47.2, C48.2, C52.2, F3.1, NT1.1, U1.5 (GNDANA)
IO_0: U1.48 (PB03); also elsewhere on the board
IO_0_OUT: R49.1; also elsewhere on the board
IO_1: U1.22 (PA13); also elsewhere on the board
IO_1_OUT: R45.1; also elsewhere on the board
JUMPER0: JP2.1, U1.1 (PA00)
OUT_0: R42.1, U1.2 (PA01); also elsewhere on the board
OUT_1: R43.1, U1.19 (PB10); also elsewhere on the board
PA20: U1.29 (PA20); also elsewhere on the board
PDEC0: U1.33 (PA24); also elsewhere on the board
PDEC1: U1.34 (PA25); also elsewhere on the board
PDEC2: U1.37 (PB22); also elsewhere on the board
RESET: R48.2; also elsewhere on the board
SPI1_CS: U1.27 (PA18); also elsewhere on the board
SPI1_MISO: U1.28 (PA19); also elsewhere on the board
SPI1_MOSI: U1.25 (PA16); also elsewhere on the board
SPI1_SCK: U1.26 (PA17); also elsewhere on the board
SWDCLK: R40.1, R51.2, U1.45 (PA30); also elsewhere on the board
SWDIO: R52.2, U1.46 (PA31); also elsewhere on the board
TEMP_0: C41.1, R39.2, U1.7 (PB08)
TEMP_1: C26.1, R72.2, U1.12 (PA07)
THERMISTOR_0: R39.1, R41.2; also elsewhere on the board
THERMISTOR_1: R72.1, R73.2; also elsewhere on the board
VDDANA: C47.1, C48.1, L6.2, R23.2, U1.6 (VDDANA)
VIN_MON: U1.3 (PA02); also elsewhere on the board
VREF_MON: C52.1, R23.1, R26.1, R41.1, R73.1, U1.9 (PA04)
VSSA: F3.2, R26.2, R27.2; also elsewhere on the board
VSSA_MON: C55.1, R27.1, U1.8 (PB09)

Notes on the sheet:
VREF Monitoring
Status LEDS
Red
Temp
Board Type
CAN RESET Jumper
Green
VSSA Sensing

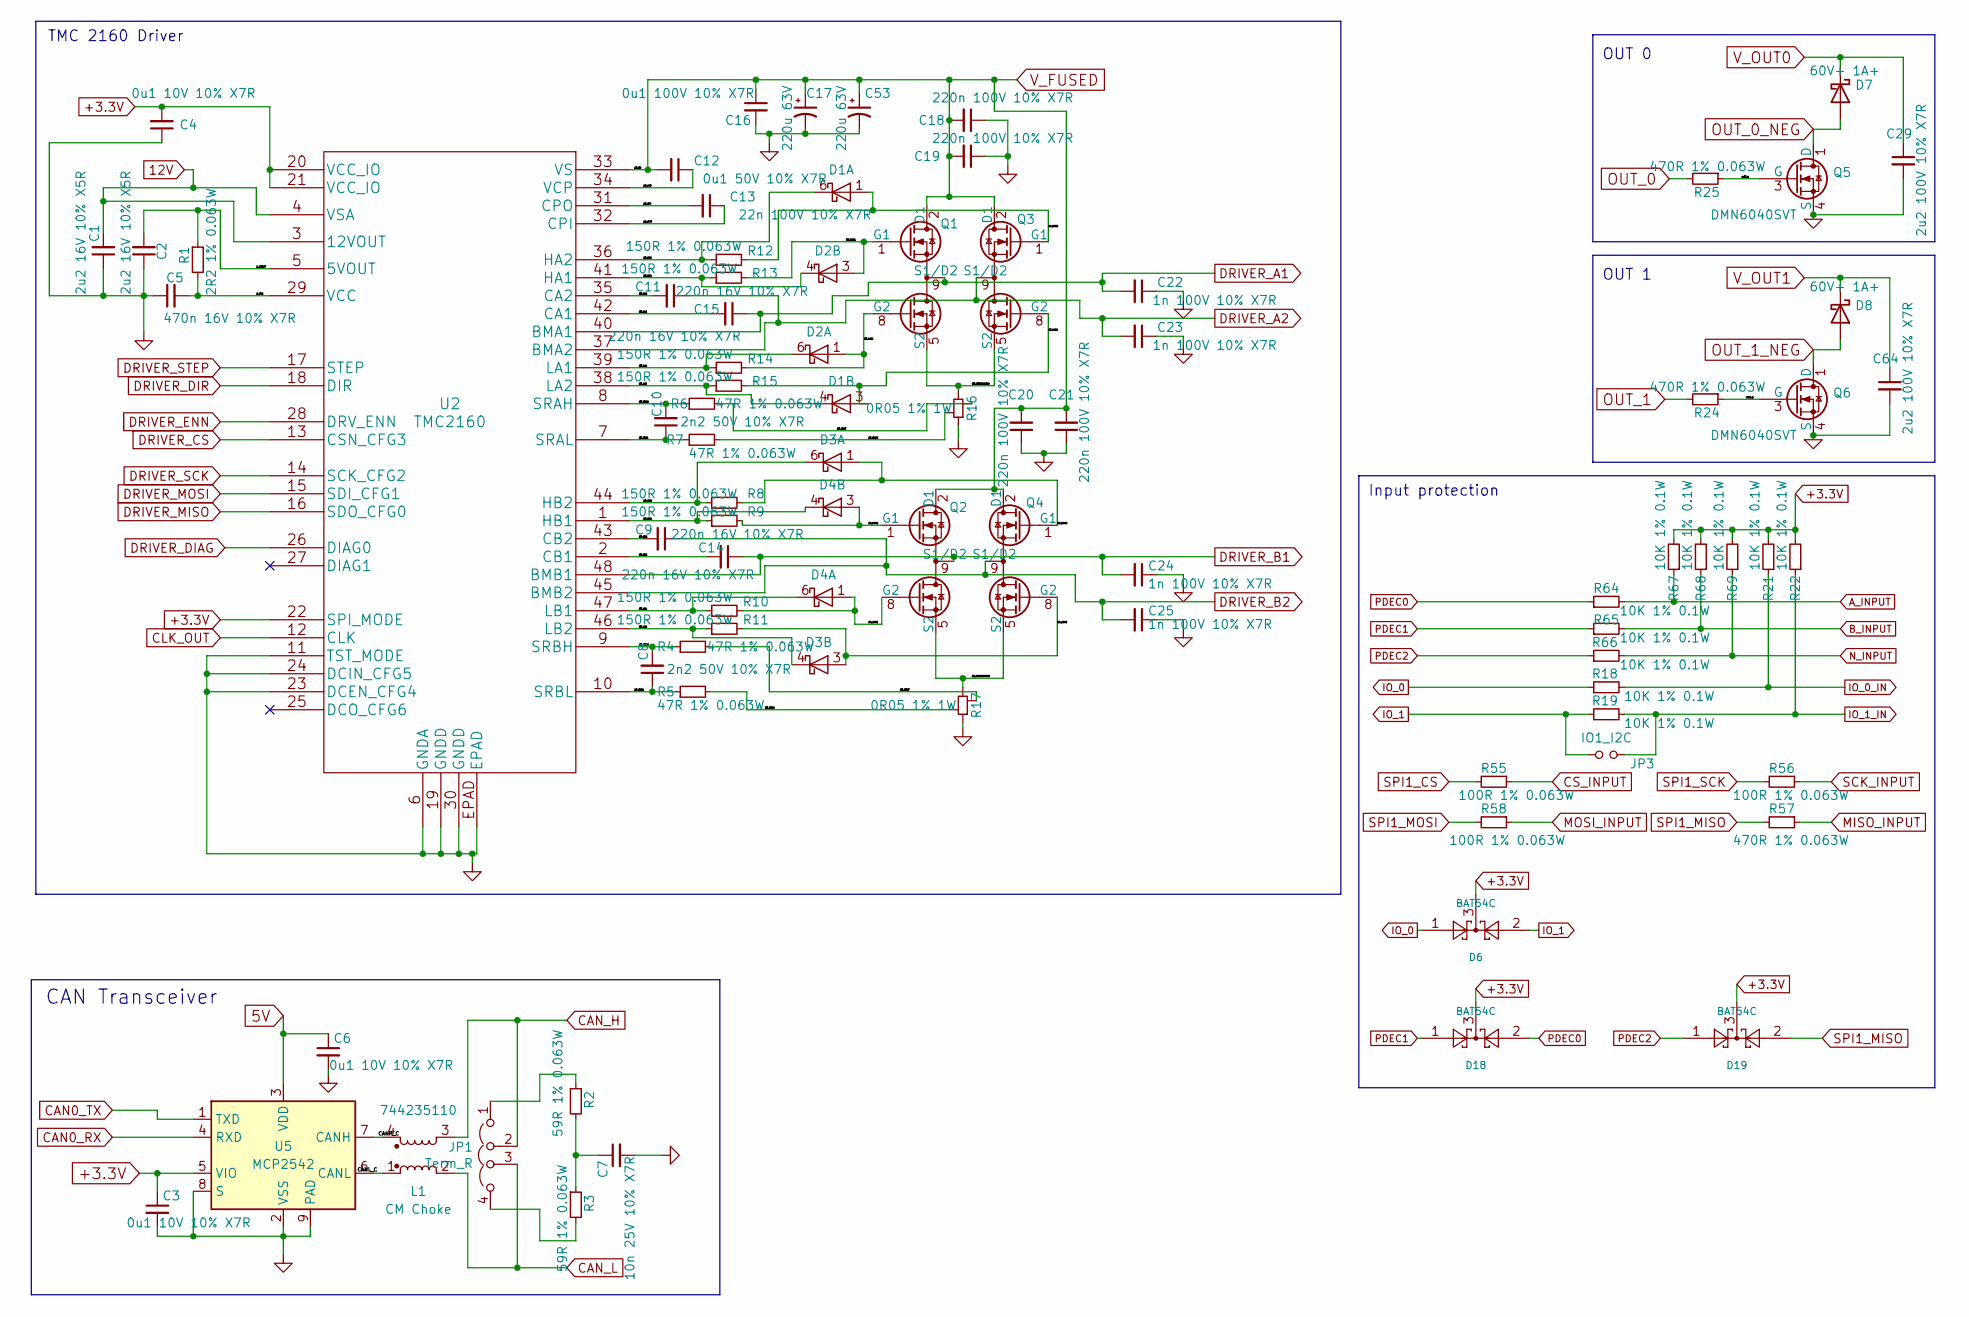
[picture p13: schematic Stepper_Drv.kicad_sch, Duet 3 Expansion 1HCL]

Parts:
C1, C2: 2u2 16V 10% X5R; C_0603_1608Metric_Wbry; Part Number CL10A225KO8NNNC
C3, C4, C6: 0u1 10V 10% X7R; C_0402_1005Metric_Wbry; Part Number CL05B104KP5NNNC
C5: 470n 16V 10% X7R; C_0603_1608Metric_Wbry; Part Number CL10B474KO8NNNC
C7: 10n 25V 10% X7R; C_0402_1005Metric_Wbry; Part Number CL05B103KA5VPNC
C8, C10: 2n2 50V 10% X7R; C_0402_1005Metric_Wbry; Part Number GCM155R71H222KA37D
C9, C11, C14, C15: 220n 16V 10% X7R; C_0603_1608Metric_Wbry; Part Number CL10B224KO8NNNC
C12: 0u1 50V 10% X7R; C_0603_1608Metric_Wbry; Part Number CL10B104KB8NNNC
C13: 22n 100V 10% X7R; C_0603_1608Metric_Wbry; Part Number C0603C223K1RACTU
C16: 0u1 100V 10% X7R; C_0603_1608Metric_Wbry; Part Number HMK107B7104MA-T or similar
C17, C53: 220u 63V; CP_Elec_12.5x14; Part Number 865060762009
C18, C19, C20, C21: 220n 100V 10% X7R; C_1206_3216Metric; Part Number C3216X7R2A224K115AA
C22, C23, C24, C25: 1n 100V 10% X7R; C_0603_1608Metric_Wbry; Part Number CGA3E2X7R2A102K080AA
C29, C64: 2u2 100V 10% X7R; C_1210_3225Metric; Part Number CL32B225KCJSNNE
D1, D2, D3, D4: BAT40V; SOT-563; Part Number BAT40V-7
D6, D18, D19: BAT54C; SOT-23; Part Number BAT54CLT1G
D7, D8: 60V+ 1A+; D_SMF; Part Number SS1FH10-M3/H or equivalent
JP1: Term_R; PinHeader_1x04_P2.54mm_Vertical; Part Number THS-04-R
JP3: IO1_I2C; PinHeader_1x02_P2.54mm_Vertical; Part Number THS-02-R
L1: CM Choke; Wurth_CM_Choke_1812_744235nnn; Part Number 744235110
Q1, Q2, Q3, Q4: SIZ250DT; Vishay_PowerPAIR3x3S; Part Number SIZ250DT-T1-GE3
Q5, Q6: DMN6040SVT; SOT-23-6-DMN6040SVT; Part Number DMN6040SVT
R1: 2R2 1% 0.063W; R_0402_1005Metric_Wbry; Part Number RMCF0402FT2R20
R2, R3: 59R 1% 0.063W; R_0402_1005Metric_Wbry; Part Number RMCF0402FT59R0
R4, R5, R6, R7: 47R 1% 0.063W; R_0603_1608Metric_Wbry; Part Number RMCF0402FT47R0
R8, R9, R10, R11, R12, R13, R14, R15: 150R 1% 0.063W; R_0402_1005Metric_Wbry; Part Number RMCF0402FT150R
R16, R17: 0R05 1% 1W; R_1206_SenseResistorKelvin; Part Number PE1206FRE470R05L or ERJ-8CWFR050V or si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
R18, R19, R21, R22, R64, R65, R66, R67, R68, R69: 10K 1% 0.1W; R_0402_1005Metric_Wbry; Part Number RK73H1ETTP1002F
R24, R25, R57: 470R 1% 0.063W; R_0402_1005Metric_Wbry; Part Number RC0402FR-07470RL
R55, R56, R58: 100R 1% 0.063W; R_0402_1005Metric_Wbry; Part Number CRGCQ0402F100R
U2: TMC2160; TMC5160-TA; Part Number TMC2160A-TA
U5: MCP2542; DFN-8-1EP_3x2mm_P0.5mm_EP1.3x1.5mm; Part Number MCP2542FDT-E/MNY

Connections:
5V: C6.1, U5.3 (VDD); also elsewhere on the board
12V: C1.2, U2.3 (12VOUT), U2.4 (VSA); also elsewhere on the board
+3.3V: C3.1, C4.2, D6.3, D18.3, D19.3, R21.2, R22.2, R67.2, R68.2, R69.2, U2.20 (VCC_IO), U2.21 (VCC_IO), U2.22 (SPI_MODE), U5.5 (VIO); also elsewhere on the board
/Stepper Driver & Endstops/CANH_C: L1.4, U5.7 (CANH)
/Stepper Driver & Endstops/CANL_C: L1.1, U5.6 (CANL)
/Stepper Driver & Endstops/D0_CA1: C15.2, U2.42 (CA1)
/Stepper Driver & Endstops/D0_CA2: C11.2, U2.35 (CA2)
/Stepper Driver & Endstops/D0_CB1: C14.2, U2.2 (CB1)
/Stepper Driver & Endstops/D0_CB2: C9.2, U2.43 (CB2)
/Stepper Driver & Endstops/D0_CPI: C13.2, U2.31 (CPO)
/Stepper Driver & Endstops/D0_CPO: C13.1, U2.32 (CPI)
/Stepper Driver & Endstops/D0_FETSOURCEA: Q1.5 (S2), Q1.6 (S2), Q1.7 (S2), Q3.5 (S2), Q3.6 (S2), Q3.7 (S2), R16.2
/Stepper Driver & Endstops/D0_FETSOURCEB: Q2.5 (S2), Q2.6 (S2), Q2.7 (S2), Q4.5 (S2), Q4.6 (S2), Q4.7 (S2), R17.2
/Stepper Driver & Endstops/D0_HA1: D2.4 (C), R13.1, U2.41 (HA1)
/Stepper Driver & Endstops/D0_HA2: D1.6 (C), R12.1, U2.36 (HA2)
/Stepper Driver & Endstops/D0_HAG1: D2.3 (A), Q1.1 (G1), R13.2
/Stepper Driver & Endstops/D0_HAG2: D1.1 (A), Q3.1 (G1), R12.2
/Stepper Driver & Endstops/D0_HB1: D4.4 (C), R9.1, U2.1 (HB1)
/Stepper Driver & Endstops/D0_HB2: D3.6 (C), R8.1, U2.44 (HB2)
/Stepper Driver & Endstops/D0_HBG1: D4.3 (A), Q2.1 (G1), R9.2
/Stepper Driver & Endstops/D0_HBG2: D3.1 (A), Q4.1 (G1), R8.2
/Stepper Driver & Endstops/D0_LA1: D2.6 (C), R14.1, U2.39 (LA1)
/Stepper Driver & Endstops/D0_LA2: D1.4 (C), R15.1, U2.38 (LA2)
/Stepper Driver & Endstops/D0_LAG1: D2.1 (A), Q1.8 (G2), R14.2
/Stepper Driver & Endstops/D0_LAG2: D1.3 (A), Q3.8 (G2), R15.2
/Stepper Driver & Endstops/D0_LB1: D4.6 (C), R10.1, U2.47 (LB1)
/Stepper Driver & Endstops/D0_LB2: D3.4 (C), R11.1, U2.46 (LB2)
/Stepper Driver & Endstops/D0_LBG1: D4.1 (A), Q2.8 (G2), R10.2
/Stepper Driver & Endstops/D0_LBG2: D3.3 (A), Q4.8 (G2), R11.2
/Stepper Driver & Endstops/D0_SRAG: R7.2, R16.3
/Stepper Driver & Endstops/D0_SRAH: C10.2, R6.1, U2.8 (SRAH)
/Stepper Driver & Endstops/D0_SRAL: C10.1, R7.1, U2.7 (SRAL)
/Stepper Driver & Endstops/D0_SRAT: R6.2, R16.4
/Stepper Driver & Endstops/D0_SRBG: R5.2, R17.3
/Stepper Driver & Endstops/D0_SRBH: C8.2, R4.1, U2.9 (SRBH)
/Stepper Driver & Endstops/D0_SRBL: C8.1, R5.1, U2.10 (SRBL)
/Stepper Driver & Endstops/D0_SRBT: R4.2, R17.4
/Stepper Driver & Endstops/D0_VCP: C12.1, U2.34 (VCP)
/Stepper Driver & Endstops/D_5VOUT: C2.2, R1.1, U2.5 (5VOUT)
/Stepper Driver & Endstops/D_VCC: C5.2, R1.2, U2.29 (VCC)
/Stepper Driver & Endstops/out0_g: Q5.3 (G), R25.1
/Stepper Driver & Endstops/out1_g: Q6.3 (G), R24.1
A_INPUT: R64.2, R67.1; also elsewhere on the board
B_INPUT: R65.2, R68.1; also elsewhere on the board
CAN0_RX: U5.4 (RXD); also elsewhere on the board
CAN0_TX: U5.1 (TXD); also elsewhere on the board
CAN_H: JP1.2 (C), L1.3; also elsewhere on the board
CAN_L: JP1.3 (C), L1.2; also elsewhere on the board
CLK_OUT: U2.12 (CLK); also elsewhere on the board
CS_INPUT: R55.1; also elsewhere on the board
DRIVER_A1: C15.1, C22.2, Q1.9 (S1/D2), U2.40 (BMA1); also elsewhere on the board
DRIVER_A2: C11.1, C23.2, Q3.9 (S1/D2), U2.37 (BMA2); also elsewhere on the board
DRIVER_B1: C14.1, C24.2, Q2.9 (S1/D2), U2.48 (BMB1); also elsewhere on the board
DRIVER_B2: C9.1, C25.2, Q4.9 (S1/D2), U2.45 (BMB2); also elsewhere on the board
DRIVER_CS: U2.13 (CSN_CFG3); also elsewhere on the board
DRIVER_DIAG: U2.26 (DIAG0); also elsewhere on the board
DRIVER_DIR: U2.18 (DIR); also elsewhere on the board
DRIVER_ENN: U2.28 (DRV_ENN); also elsewhere on the board
DRIVER_MISO: U2.16 (SDO_CFG0); also elsewhere on the board
DRIVER_MOSI: U2.15 (SDI_CFG1); also elsewhere on the board
DRIVER_SCK: U2.14 (SCK_CFG2); also elsewhere on the board
DRIVER_STEP: U2.17 (STEP); also elsewhere on the board
GND: C1.1, C2.1, C3.2, C4.1, C5.1, C6.2, C7.2, C16.2, C17.2, C18.1, C19.1, C20.1, C21.1, C22.1, C23.1, C24.1, C25.1, C29.2, C53.2, C64.2, Q5.4 (S), Q6.4 (S), R16.1, R17.1, U2.6 (GNDA), U2.11 (TST_MODE), U2.19 (GNDD), U2.23 (DCEN_CFG4), U2.24 (DCIN_CFG5), U2.30 (GNDD), U2.EPAD, U5.2 (VSS), U5.8 (S), U5.9 (PAD); also elsewhere on the board
IO_0: D6.1, R18.1; also elsewhere on the board
IO_0_IN: R18.2, R21.1; also elsewhere on the board
IO_1: D6.2, JP3.1, R19.1; also elsewhere on the board
IO_1_IN: JP3.2, R19.2, R22.1; also elsewhere on the board
MISO_INPUT: R57.1; also elsewhere on the board
MOSI_INPUT: R58.1; also elsewhere on the board
N_INPUT: R66.2, R69.1; also elsewhere on the board
unnamed: C7.1, R2.2, R3.1
unnamed: JP1.1 (A), R2.1
unnamed: JP1.4 (B), R3.2
OUT_0: R25.2; also elsewhere on the board
OUT_0_NEG: D7.2 (A), Q5.1 (D), Q5.2 (D), Q5.5 (D), Q5.6 (D); also elsewhere on the board
OUT_1: R24.2; also elsewhere on the board
OUT_1_NEG: D8.2 (A), Q6.1 (D), Q6.2 (D), Q6.5 (D), Q6.6 (D); also elsewhere on the board
PDEC0: D18.2, R64.1; also elsewhere on the board
PDEC1: D18.1, R65.1; also elsewhere on the board
PDEC2: D19.1, R66.1; also elsewhere on the board
SCK_INPUT: R56.1; also elsewhere on the board
SPI1_CS: R55.2; also elsewhere on the board
SPI1_MISO: D19.2, R57.2; also elsewhere on the board
SPI1_MOSI: R58.2; also elsewhere on the board
SPI1_SCK: R56.2; also elsewhere on the board
V_FUSED: C12.2, C16.1, C17.1, C18.2, C19.2, C20.2, C21.2, C53.1, Q1.2 (D1), Q1.3 (D1), Q1.4 (D1), Q1.10 (D1), Q2.2 (D1), Q2.3 (D1), Q2.4 (D1), Q2.10 (D1), Q3.2 (D1), Q3.3 (D1), Q3.4 (D1), Q3.10 (D1), Q4.2 (D1), Q4.3 (D1), Q4.4 (D1), Q4.10 (D1), U2.33 (VS); also elsewhere on the board
V_OUT0: C29.1, D7.1 (K); also elsewhere on the board
V_OUT1: C64.1, D8.1 (K); also elsewhere on the board

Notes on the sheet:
Input protection
OUT 0
CAN Transceiver
TMC 2160 Driver
OUT 1

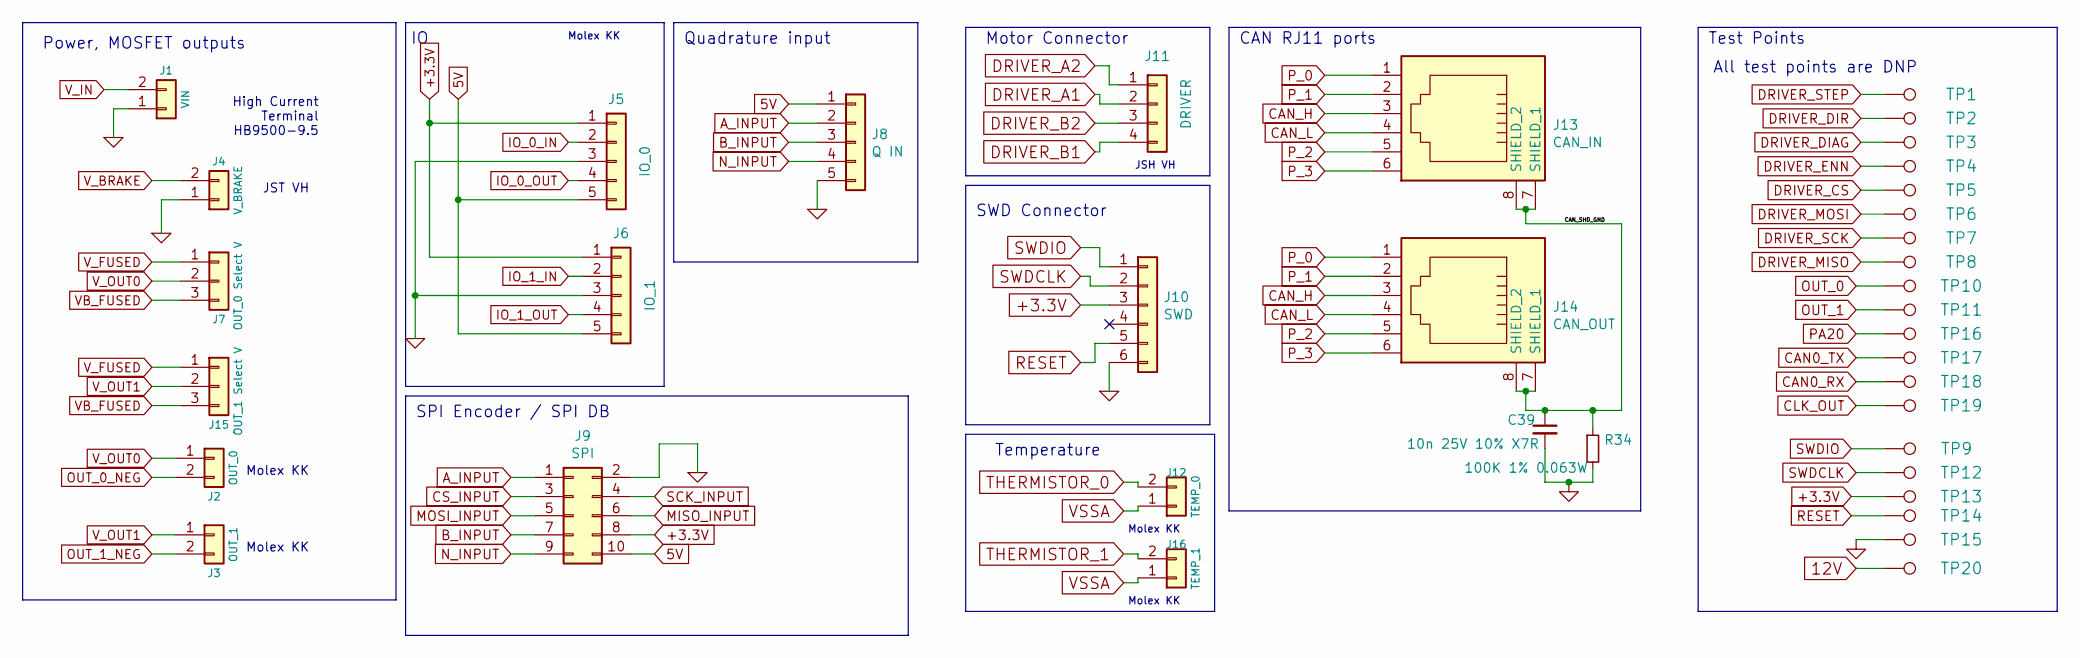
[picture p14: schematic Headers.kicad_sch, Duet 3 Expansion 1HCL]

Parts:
C39: 10n 25V 10% X7R; C_0402_1005Metric_Wbry; Part Number CL05B103KA5VPNC
J1: VIN; screwt-barrier-9.5mm-1x2; Part Number HB950-9.50-2P
J2: OUT_0; Wurth_61900211121-1x02_P2.54mm_Vertical-(Molex_KK-254_AE-64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; Part Number 61900211121
J3: OUT_1; Wurth_61900211121-1x02_P2.54mm_Vertical-(Molex_KK-254_AE-64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; Part Number 61900211121
J4: V_BRAKE; JST_VH_B2P-VH_1x02_P3.96mm_Vertical; Part Number B2P-VH(LF)(SN)
J5: IO_0; Wurth_61900511121-1x05_P2.54mm_Vertical(Molex_KK-254_AE-641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; Part Number 61900511121
J6: IO_1; Wurth_61900511121-1x05_P2.54mm_Vertical(Molex_KK-254_AE-641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; Part Number 61900511121
J7: OUT_0 Select V; PinHeader_1x03_P2.54mm_Vertical; Part Number THS-03-R
J8: Q IN; Wurth_61900511121-1x05_P2.54mm_Vertical(Molex_KK-254_AE-641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; Part Number 61900511121
J9: SPI; IDC-Header_2x05_P2.54mm_Vertical; Part Number 61201021621
J10: SWD; JST_ZH_1x06_P1.5_B6B-ZR-SM4-TF; Part Number B6B-ZR(LF)(SN)
J11: DRIVER; JST_VH_B4P-VH_1x04_P3.96mm_Vertical; Part Number B4P-VH(LF)(SN)
J12: TEMP_0; Wurth_61900211121-1x02_P2.54mm_Vertical-(Molex_KK-254_AE-64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; Part Number 61900211121
J13: CAN_IN; RJ11_6P6C_half_shield; Part Number Wurth 615 006 143 421 or equivalent
J14: CAN_OUT; RJ11_6P6C_half_shield; Part Number Wurth 615 006 143 421 or equivalent
J15: OUT_1 Select V; PinHeader_1x03_P2.54mm_Vertical; Part Number THS-03-R
J16: TEMP_1; Wurth_61900211121-1x02_P2.54mm_Vertical-(Molex_KK-254_AE-64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; Part Number 61900211121
R34: 100K 1% 0.063W; R_0402_1005Metric_Wbry; Part Number RMCF0402FT100K
TP1: STEP; TestPoint_Pad_D2.0mm; Part Number virtual component - DNP
TP2: DIR; TestPoint_Pad_D2.0mm; Part Number virtual component - DNP
TP3: DIAG; TestPoint_Pad_D2.0mm; Part Number virtual component - DNP
TP4: ENN; TestPoint_Pad_D2.0mm; Part Number virtual component - DNP
TP5: D_CS; TestPoint_Pad_D2.0mm; Part Number virtual component - DNP
TP6: D_MOSI; TestPoint_Pad_D2.0mm; Part Number virtual component - DNP
TP7: D_SCK; TestPoint_Pad_D2.0mm; Part Number virtual component - DNP
TP8: D_MISO; TestPoint_Pad_D2.0mm; Part Number virtual component - DNP
TP9: SWDIO; TestPoint_Pad_D2.0mm; Part Number virtual component - DNP
TP10: OUT_0; TestPoint_Pad_D2.0mm; Part Number virtual component - DNP
TP11: OUT_1; TestPoint_Pad_D2.0mm; Part Number virtual component - DNP
TP12: SWDCLK; TestPoint_Pad_D2.0mm; Part Number virtual component - DNP
TP13: +3.3V; TestPoint_Pad_D2.0mm; Part Number virtual component - DNP
TP14: RST; TestPoint_Pad_D2.0mm; Part Number virtual component - DNP
TP15: GND; TestPoint_Pad_D2.0mm; Part Number virtual component - DNP
TP16: PA20; TestPoint_Pad_D2.0mm; Part Number virtual component - DNP
TP17: CAN0_TX; TestPoint_Pad_D2.0mm; Part Number virtual component - DNP
TP18: CAN0_RX; TestPoint_Pad_D2.0mm; Part Number virtual component - DNP
TP19: CLK_OUT; TestPoint_Pad_D2.0mm; Part Number virtual component - DNP
TP20: 12V; TestPoint_Pad_D2.0mm; Part Number virtual component - DNP

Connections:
5V: J5.5, J6.5, J8.1, J9.10; also elsewhere on the board
12V: TP20.1; also elsewhere on the board
+3.3V: J5.1, J6.1, J9.8, J10.3, TP13.1; also elsewhere on the board
/Headers/CAN_SHD_GND: C39.1, J13.7 (SHIELD_1), J13.8 (SHIELD_2), J14.7 (SHIELD_1), J14.8 (SHIELD_2), R34.1
A_INPUT: J8.2, J9.1; also elsewhere on the board
B_INPUT: J8.3, J9.7; also elsewhere on the board
CAN0_RX: TP18.1; also elsewhere on the board
CAN0_TX: TP17.1; also elsewhere on the board
CAN_H: J13.3, J14.3; also elsewhere on the board
CAN_L: J13.4, J14.4; also elsewhere on the board
CLK_OUT: TP19.1; also elsewhere on the board
CS_INPUT: J9.3; also elsewhere on the board
DRIVER_A1: J11.2; also elsewhere on the board
DRIVER_A2: J11.1; also elsewhere on the board
DRIVER_B1: J11.4; also elsewhere on the board
DRIVER_B2: J11.3; also elsewhere on the board
DRIVER_CS: TP5.1; also elsewhere on the board
DRIVER_DIAG: TP3.1; also elsewhere on the board
DRIVER_DIR: TP2.1; also elsewhere on the board
DRIVER_ENN: TP4.1; also elsewhere on the board
DRIVER_MISO: TP8.1; also elsewhere on the board
DRIVER_MOSI: TP6.1; also elsewhere on the board
DRIVER_SCK: TP7.1; also elsewhere on the board
DRIVER_STEP: TP1.1; also elsewhere on the board
GND: C39.2, J1.1, J4.1, J5.3, J6.3, J8.5, J9.2, J10.6, R34.2, TP15.1; also elsewhere on the board
IO_0_IN: J5.2; also elsewhere on the board
IO_0_OUT: J5.4; also elsewhere on the board
IO_1_IN: J6.2; also elsewhere on the board
IO_1_OUT: J6.4; also elsewhere on the board
MISO_INPUT: J9.6; also elsewhere on the board
MOSI_INPUT: J9.5; also elsewhere on the board
N_INPUT: J8.4, J9.9; also elsewhere on the board
OUT_0: TP10.1; also elsewhere on the board
OUT_0_NEG: J2.2; also elsewhere on the board
OUT_1: TP11.1; also elsewhere on the board
OUT_1_NEG: J3.2; also elsewhere on the board
PA20: TP16.1; also elsewhere on the board
P_0: J13.1, J14.1
P_1: J13.2, J14.2
P_2: J13.5, J14.5
P_3: J13.6, J14.6
RESET: J10.5, TP14.1; also elsewhere on the board
SCK_INPUT: J9.4; also elsewhere on the board
SWDCLK: J10.2, TP12.1; also elsewhere on the board
SWDIO: J10.1, TP9.1; also elsewhere on the board
THERMISTOR_0: J12.2; also elsewhere on the board
THERMISTOR_1: J16.2; also elsewhere on the board
VB_FUSED: J7.3, J15.3; also elsewhere on the board
VSSA: J12.1, J16.1; also elsewhere on the board
V_BRAKE: J4.2; also elsewhere on the board
V_FUSED: J7.1, J15.1; also elsewhere on the board
V_IN: J1.2; also elsewhere on the board
V_OUT0: J2.1, J7.2; also elsewhere on the board
V_OUT1: J3.1, J15.2; also elsewhere on the board

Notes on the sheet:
Motor Connector
JSH VH
All test points are DNP
Power, MOSFET outputs
High Current Terminal HB9500-9.5
JST VH
Molex KK
Test Points
SPI Encoder / SPI DB
Quadrature input
CAN RJ11 ports
Temperature
SWD Connector

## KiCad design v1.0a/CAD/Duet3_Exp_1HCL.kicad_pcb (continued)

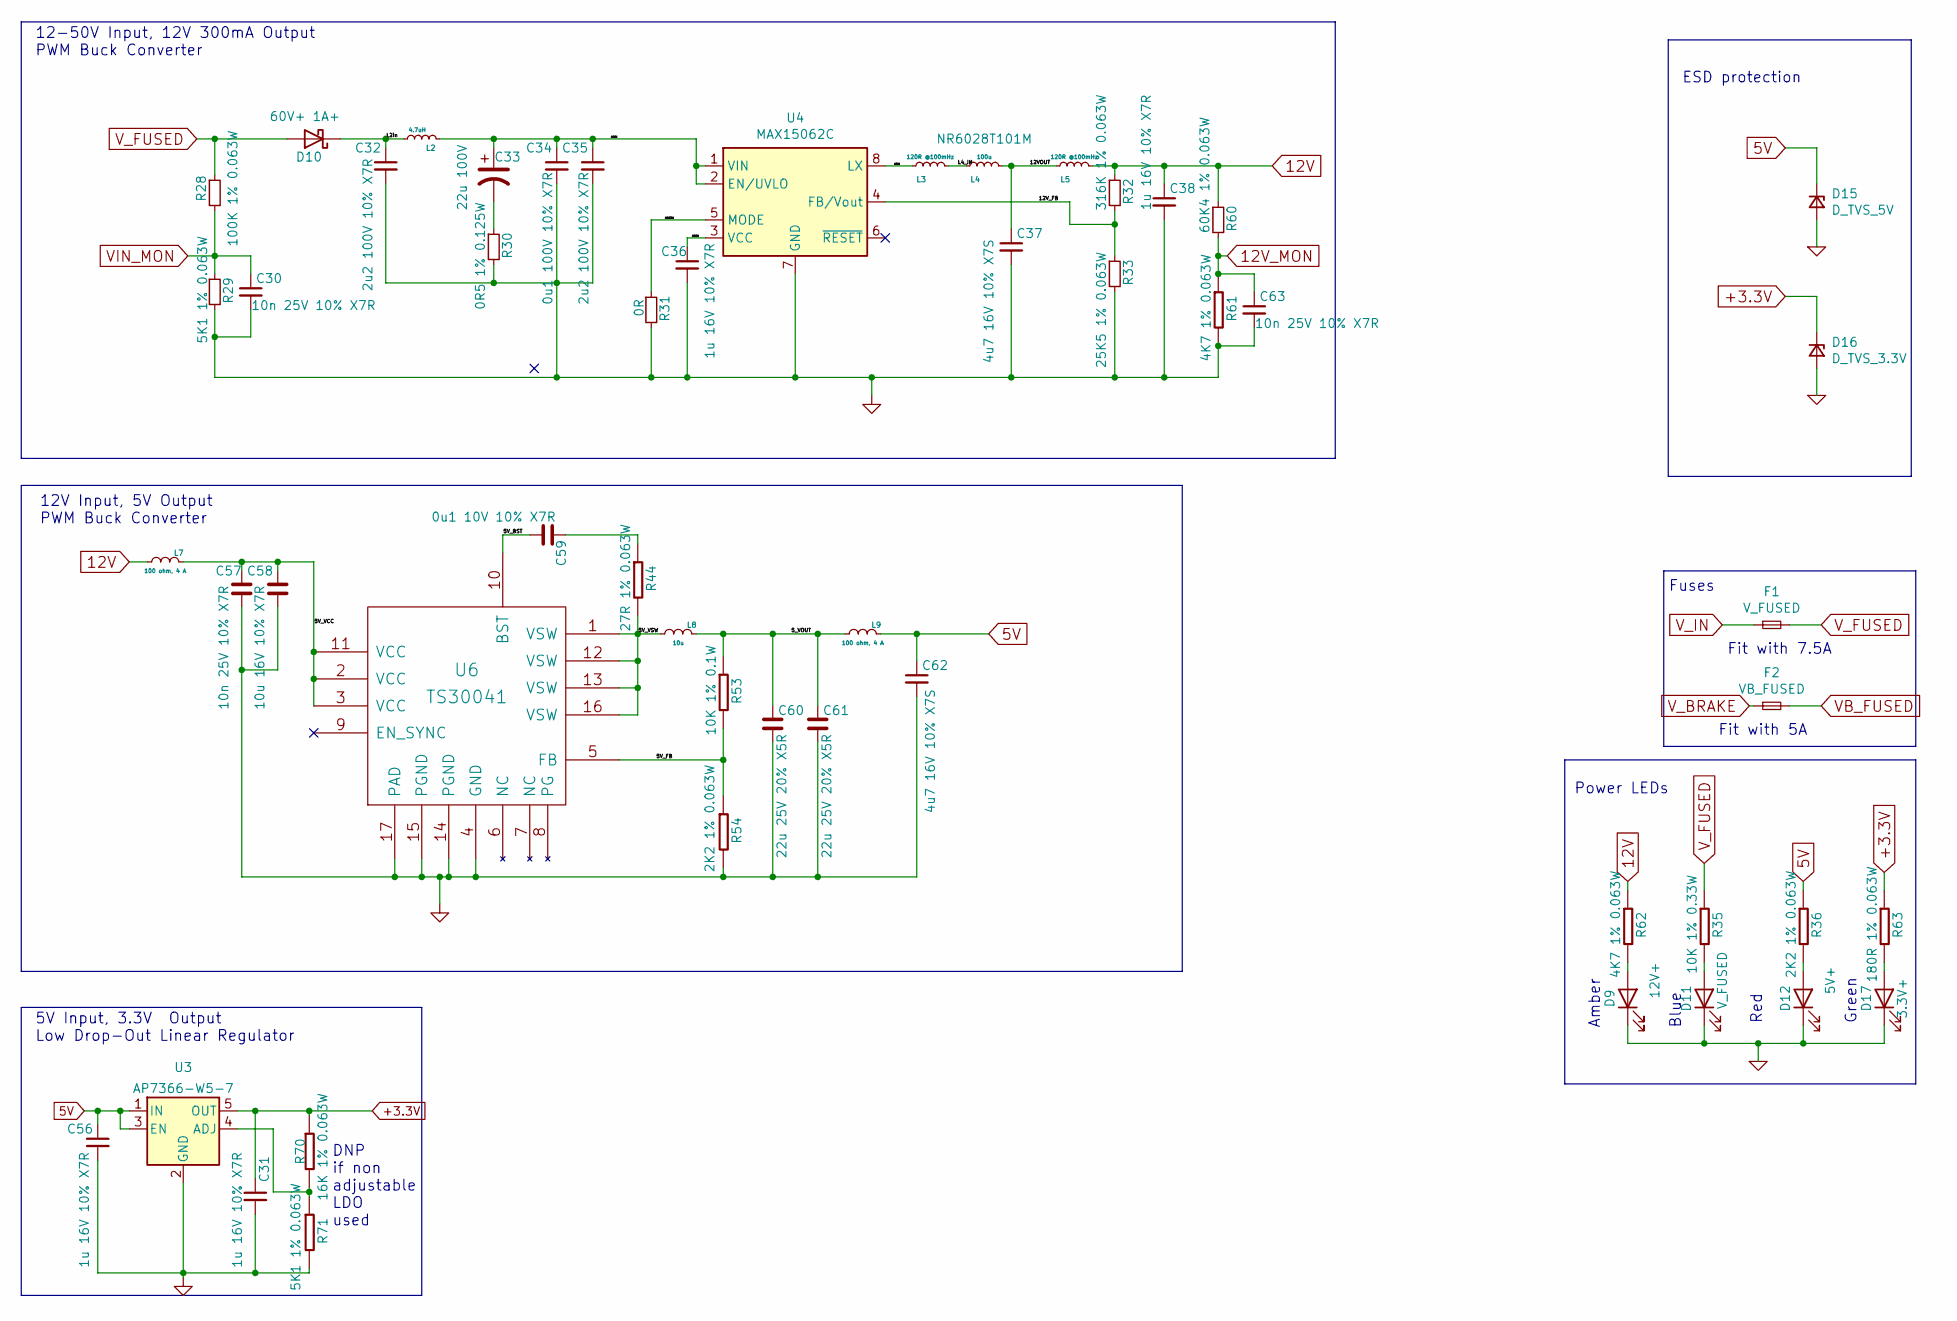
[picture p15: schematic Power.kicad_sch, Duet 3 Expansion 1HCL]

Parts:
C30, C57, C63: 10n 25V 10% X7R; C_0402_1005Metric_Wbry; Part Number CL05B103KA5VPNC
C31, C36, C38, C56: 1u 16V 10% X7R; C_0603_1608Metric_Wbry; Part Number CL10B105KO8NNNC
C32, C35: 2u2 100V 10% X7R; C_1210_3225Metric; Part Number CL32B225KCJSNNE
C33: 22u 100V; CP_Elec_8x10; Part Number EEE-2AA220UP or similar
C34: 0u1 100V 10% X7R; C_0603_1608Metric_Wbry; Part Number HMK107B7104MA-T or similar
C37, C62: 4u7 16V 10% X7S; C_1206_3216Metric; Part Number GRM21BR71C475KE51K
C58: 10u 16V 10% X7R; C_0805_2012Metric; Part Number CL21B106KOQNNNE
C59: 0u1 10V 10% X7R; C_0402_1005Metric_Wbry; Part Number CL05B104KP5NNNC
C60, C61: 22u 25V 20% X5R; C_0805_2012Metric; Part Number GRM21BR61E226ME44L
D9: 12V+; LED_0603_1608Metric; Part Number 150060AS75000 or equivalent Amber
D10: 60V+ 1A+; D_SMF; Part Number SS1FH10-M3/H or equivalent
D11: V_FUSED; LED_0603_1608Metric; Part Number 150060BS75000 or equivalent Blue
D12: 5V+; LED_0603_1608Metric; Part Number 150060RS75000 or equivalent Red
D15: D_TVS_5V; DFN1610-2L; Part Number 824032815 or 824031815
D16: D_TVS_3.3V; DFN1610-2L; Part Number 824032813
D17: 3.3V+; LED_0603_1608Metric; Part Number 150060VS75000 or equivalent Green
F1: V_FUSED; MCCQ-122-minibladefuseholder; Part Number Fit with 5A Fuse
F2: VB_FUSED; MCCQ-122-minibladefuseholder; Part Number Fit with 5A Fuse
L2: 4.7uH; L_0805_2012Metric; Part Number MBKK2012T4R7M or CB2012T4R7M or similar
L3, L5: 120R @100mHz; L_0402_1005Metric; Part Number 7427927311 or similar
L4: 100u; L_Taiyo-Yuden_NR-60xx; Rating >0.5A, >0.6A saturation, shielded, <0R8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; Part Number NR6028T101M
L7, L9: 100 ohm, 4 A; L_0805_2012Metric; Part Number 742792025 or MPZ2012S101A or similar
L8: 10u; L_Wuerth_7440405xxxx; Part Number 74404054100 or NR5040T100M
R28: 100K 1% 0.063W; R_0402_1005Metric_Wbry; Part Number RMCF0402FT100K
R29, R71: 5K1 1% 0.063W; R_0402_1005Metric_Wbry; Part Number RMCF0402FT5K10
R30: 0R5 1% 0.125W; R_0402_1005Metric_Wbry; Part Number CSR0402FKR500
R31: 0R; R_0402_1005Metric_Wbry; Part Number RMCF0402ZT0R00
R32: 316K 1% 0.063W; R_0402_1005Metric_Wbry; Part Number RC0402FR-07316KL
R33: 25K5 1% 0.063W; R_0402_1005Metric_Wbry; Part Number AC0402FR-0725K5L
R35: 10K 1% 0.33W; R_0805_2012Metric; Part Number CRGH0805F10K
R36, R54: 2K2 1% 0.063W; R_0402_1005Metric_Wbry; Part Number RK73H1ETTP2201F
R44: 27R 1% 0.063W; R_0402_1005Metric_Wbry; Rating 0.1W+; Part Number CRGCQ0402F27R
R53: 10K 1% 0.1W; R_0402_1005Metric_Wbry; Part Number RK73H1ETTP1002F
R60: 60K4 1% 0.063W; R_0402_1005Metric_Wbry; Part Number RMCF0402FT60K4
R61, R62: 4K7 1% 0.063W; R_0402_1005Metric_Wbry; Part Number RK73H1ETTP4701F
R63: 180R 1% 0.063W; R_0402_1005Metric_Wbry; Part Number RMCF0402FT180R
R70: 16K 1% 0.063W; R_0402_1005Metric_Wbry; Part Number RMCF0402FT16K0
U3: AP7366-W5-7; SOT-23-5; Part Number AP7366-W5-7
U4: MAX15062C; DFN-8_2x2mm_P0.5mm; Part Number MAX15062C
U6: TS30041; QFN-16-1EP_3x3mm_P0.5mm_EP1.8x1.8mm_ThermalVias; Part Number TS30041-M000QFNR

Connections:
5V: C56.1, C62.1, D15.1 (K), L9.1 (A), R36.1, U3.1 (IN), U3.3 (EN); also elsewhere on the board
12V: C38.1, L5.2, L7.2 (B), R32.1, R60.1, R62.1; also elsewhere on the board
12V_MON: C63.1, R60.2, R61.1; also elsewhere on the board
+3.3V: C31.1, D16.1 (K), R63.1, R70.1, U3.5 (OUT); also elsewhere on the board
/Power/5V_BST: C59.2, U6.10 (BST)
/Power/5V_FB: R53.2, R54.1, U6.5 (FB)
/Power/5V_VCC: C57.1, C58.1, L7.1 (A), U6.2 (VCC), U6.3 (VCC), U6.11 (VCC)
/Power/5V_VSW: L8.2 (B), R44.2, U6.1 (VSW), U6.12 (VSW), U6.13 (VSW), U6.16 (VSW)
/Power/5_VOUT: C60.1, C61.1, L8.1 (A), L9.2 (B), R53.1
/Power/12LX: L3.1, U4.8 (LX)
/Power/12MODE: R31.1, U4.5 (MODE)
/Power/12VCC: C36.1, U4.3 (VCC)
/Power/12VIN: C33.1, C34.1, C35.1, L2.2, U4.1 (VIN), U4.2 (EN/UVLO)
/Power/12VOUT: C37.1, L4.2, L5.1
/Power/12V_FB: R32.2, R33.1, U4.4 (FB/Vout)
/Power/L2in: C32.1, D10.1 (K), L2.1
/Power/L4_IN: L3.2, L4.1
GND: C30.2, C31.2, C32.2, C34.2, C35.2, C36.2, C37.2, C38.2, C56.2, C57.2, C58.2, C60.2, C61.2, C62.2, C63.2, D9.1 (K), D11.1 (K), D12.1 (K), D15.2 (A), D16.2 (A), D17.1 (K), R29.2, R30.2, R31.2, R33.2, R54.2, R61.2, R71.2, U3.2 (GND), U4.7 (GND), U6.4 (GND), U6.14 (PGND), U6.15 (PGND), U6.17 (PAD); also elsewhere on the board
unnamed: C33.2, R30.1
unnamed: C59.1, R44.1
unnamed: D9.2 (A), R62.2
unnamed: D11.2 (A), R35.2
unnamed: D12.2 (A), R36.2
unnamed: D17.2 (A), R63.2
unnamed: R70.2, R71.1, U3.4 (ADJ)
VB_FUSED: F2.2; also elsewhere on the board
VIN_MON: C30.1, R28.2, R29.1; also elsewhere on the board
V_BRAKE: F2.1; also elsewhere on the board
V_FUSED: D10.2 (A), F1.2, R28.1, R35.1; also elsewhere on the board
V_IN: F1.1; also elsewhere on the board

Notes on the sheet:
Fit with 7.5A
5V Input, 3.3V Output Low Drop-Out Linear Regulator
12V Input, 5V Output PWM Buck Converter
Power LEDs
Fit with 5A
Fuses
Amber
12-50V Input, 12V 300mA Output PWM Buck Converter
ESD protection
DNP if non adjustable LDO used
Blue
Red
Green

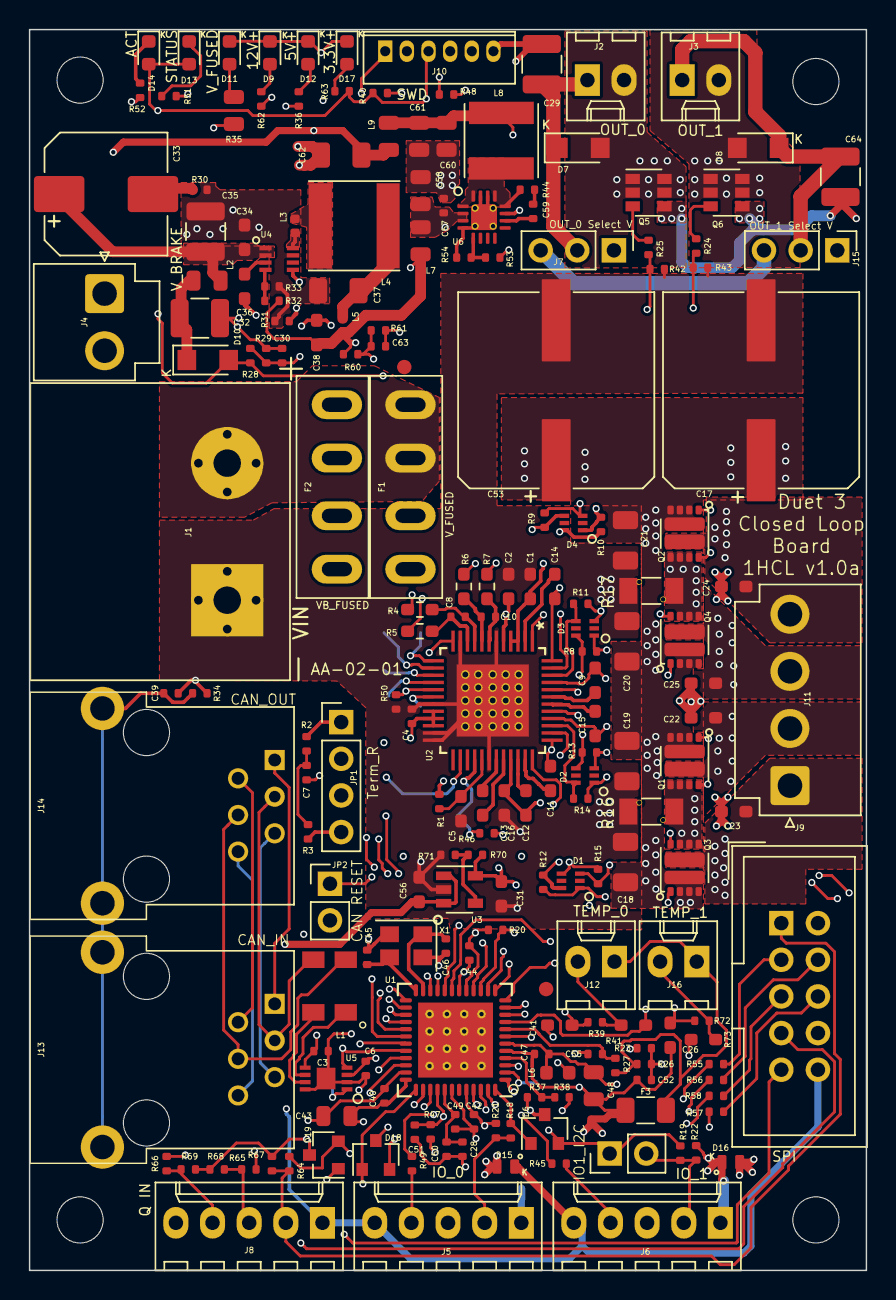
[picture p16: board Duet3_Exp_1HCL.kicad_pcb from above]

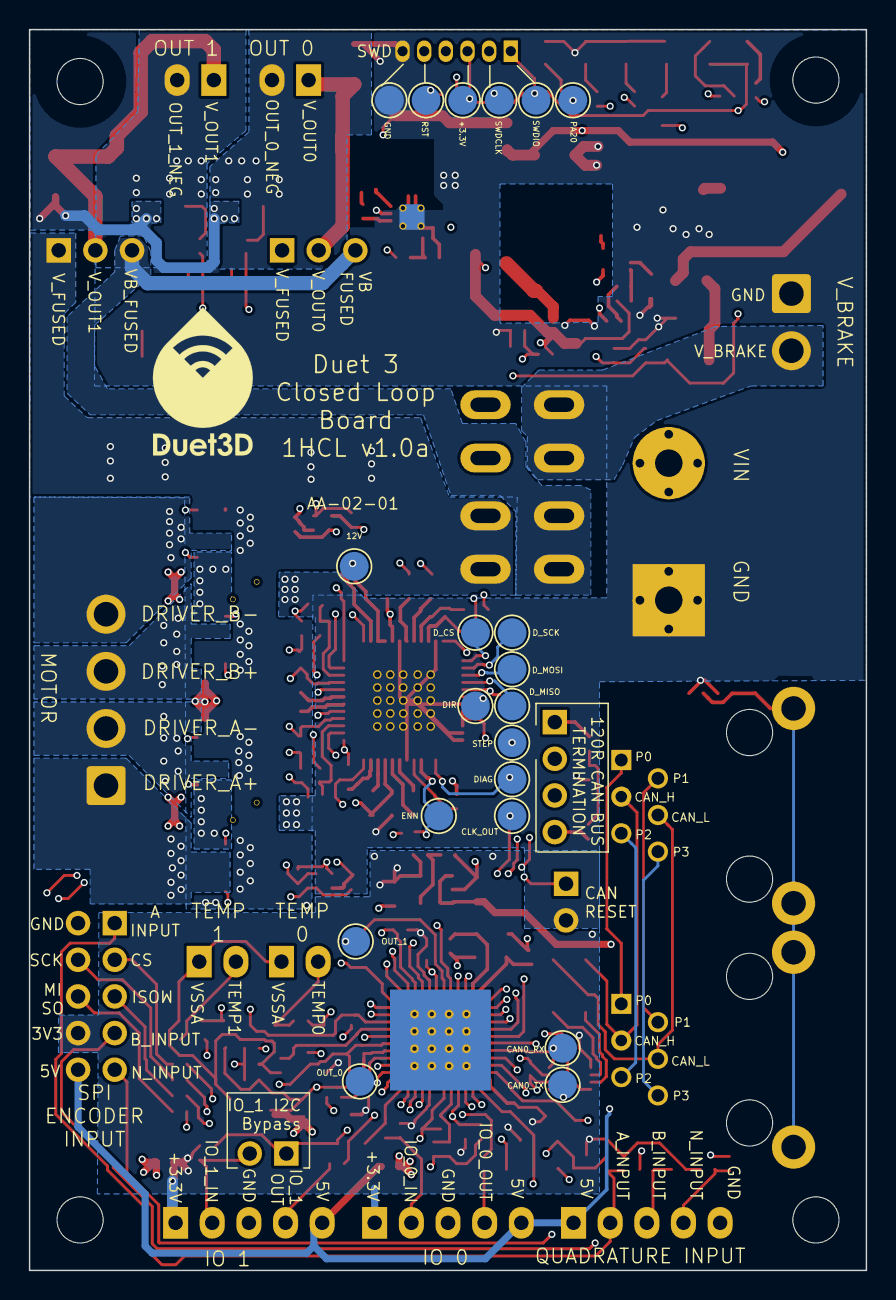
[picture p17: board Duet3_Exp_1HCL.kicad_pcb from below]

Board: 4 copper layers, 58.0 x 86.0 mm, 224 parts (21 on the bottom side), 143 nets.
